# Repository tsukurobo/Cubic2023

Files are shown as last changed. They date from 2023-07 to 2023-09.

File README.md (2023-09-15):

**目次**

- [Cubic2023](#cubic2023)
  - [概要](#概要)
    - [コメント](#コメント)
- [Cubic2023\_Shield](#cubic2023_shield)
  - [概要](#概要-1)
    - [encoder pull up](#encoder-pull-up)
    - [increment encoder cognition](#increment-encoder-cognition)
    - [inverter(NOT)](#inverternot)
    - [increment RP2040](#increment-rp2040)
    - [increment connecter](#increment-connecter)
    - [absolute encoder cognition](#absolute-encoder-cognition)
    - [absolute RP2040](#absolute-rp2040)
    - [absolute connector](#absolute-connector)
    - [decoupling capacitor](#decoupling-capacitor)
    - [Arduino nano 33 BLE](#arduino-nano-33-ble)
    - [to MotherBoard](#to-motherboard)
- [Cubic2023\_DCMotorDriver](#cubic2023_dcmotordriver)
  - [概要](#概要-2)
    - [connector](#connector)
    - [pull down](#pull-down)
    - [A3921](#a3921)
    - [current sensor](#current-sensor)
    - [Filter](#filter)
    - [DeadTime](#deadtime)
    - [Protection Circuit](#protection-circuit)
    - [for motor connection](#for-motor-connection)
    - [Bootstrap Chargepump](#bootstrap-chargepump)
    - [Indication Circuit](#indication-circuit)
    - [V5 Circuit](#v5-circuit)
    - [Decoupling Condenser](#decoupling-condenser)
    - [Bridge](#bridge)
    - [pull up](#pull-up)
    - [error lamp](#error-lamp)
    - [PS](#ps)
    - [BD63150](#bd63150)
    - [Protection Circuit](#protection-circuit-1)
    - [Indication Circuit](#indication-circuit-1)
    - [VREF](#vref)
    - [for solenoid valve](#for-solenoid-valve)
- [Cubic2023\_RP2040](#cubic2023_rp2040)
  - [概要](#概要-3)
    - [RP2040](#rp2040)
    - [bypass condenser](#bypass-condenser)
    - [surge protection](#surge-protection)
    - [connector](#connector-1)
    - [indicator](#indicator)
    - [RESET switch](#reset-switch)
    - [microUSB](#microusb)
    - [QSPI NOR flash](#qspi-nor-flash)
    - [crystal](#crystal)

# Cubic2023

## 概要
つくばろぼっとサークルではNHK学生ロボコンに向けて統合型基板を製作しており、mainがNHK学生ロボコン2023において使用したバージョンです。
回路図の説明やブロック分けなどが出来ておらず、分かりにくい状態です。※修正中

### コメント
修正中です。8/10程度を目途に進めています。

# Cubic2023_Shield
## 概要
メインマイコンを搭載する基板です。メインマイコンには以下の理由からArduino nano 33 BLE(以下：AN33BLE)を採用しました。
- 32bitマイコン
- 浮動小数点演算ユニット搭載
- 書き込み環境の構築が容易

また、AN33BLEはIMUを搭載している点もメリットです。実際には用いていないため精度は不明ですが、基板面積という点では確実にプラスです。

センサとしては、8つのインクリメンタルエンコーダと8つのアブソリュートエンコーダを接続できるように設計しました。

### encoder pull up
インクリメントエンコーダに接続しているA相B相Z相をプルアップしています。

### increment encoder cognition
インクリメントエンコーダは、Z相の多くの範囲でLOWを返すため、NOT回路によりHIGHになり、LEDが光る仕組みです。Z相をプルアップしてるため、未接続の場合LEDは光りません。A相B相が断線してる場合、LEDは光りますが正常に認識されるとは限りません。何番のエンコーダに接続してるか簡易的に確認するための機能です。

### inverter(NOT)
インクリメントエンコーダの波形を整形するインバータ（バッファ）です。NOT回路と等価なので信号が反転します。A相B相は反転しても大きな影響はないですが、Z相はhighの時間が長くなります。長い信号線を介してセンシングするためチャタリング防止などの観点から挿入しました。また、5VトレラントのICを介することで5V信号を3.3Vで駆動するRP2040に入力できるようにしています。

### increment RP2040
インクリメントエンコーダを読み取り値を記録、メインマイコンの要求に応じて状態を返すためのマイコンです。インクリメントエンコーダの読み取りは割り込み処理を必要とするため、メインマイコンと分離したいと考え、この設計にしました。

### increment connecter
ラッチ付かつサイズが小さいコネクタが望ましかったため、PAコネクタを採用しました。**AMT102/103**を接続することを想定して、ピンの順番を設定しています。

### absolute encoder cognition
アブソリュートエンコーダとのSPI通信が確立した場合にRP2040がGPIOを操作しLEDを点灯させることが出来るようにしました。

### absolute RP2040
アブソリュートエンコーダと通信をして値を記録、メインマイコンの要求に応じて状態を返すためのマイコンです。メインマイコンをmasterとしたSPIバスとは別に、absolute RP2040をmasterとしたエンコーダとの通信用のSPIバスを用意しています。

### absolute connector
こちらもPAコネクタを採用しています。**AMT223**を接続することを想定して、ピンの順番を設定しています。

### decoupling capacitor
基板上のICなどのバイパスコンデンサです。配線を引き延ばすためエンコーダのコネクタ近くにも配置しました。

### Arduino nano 33 BLE
メインマイコンです。enableをHIGHにすることでシステムを起動することができます。RESETをLOWにすることでエンコーダ用のRP2040をリセットさせることできます。他はSPI通信用のGPIOです。

### to MotherBoard
電源、SPI通信、シャットダウン信号を共有しています。

### emergency shutdown
緊急停止スイッチ接続することでシステムを起動できます。LEDにより起動状態を表示しています。

### 3-state buffer
SPI通信のslave側は通信していないときはMISOをオープンにする仕様ですが、RP2040はLOWを出力してしまい、複数slave運用がデフォルトで不可能であったため、3-state bufferを付加することで対策しました。

# Cubic2023_DCMotorDriver
## 概要
RZ-735クラスのDCモータを2基、RS-555クラスのDCモータを1基、24Vで駆動することが出来る基板です。以下ではRZ-735を想定したチャネルをメインチャネル、他方をサブチャネルと呼称します。

メインチャネルではICにA3921を採用しています。サブチャネルではICにBD63150を採用しています。データシートを参考に作成しました。データシートに載っている内容は説明を省略します。

サブチャネルはハーフブリッジ×2と見なすことで電磁弁を制御することも出来ます。

https://www.allegromicro.com/ja-jp/products/motor-drivers/brush-dc-motor-drivers/a3921

https://www.rohm.co.jp/products/motor-actuator-drivers/dc-brush-motor/bd63150afm-product

### connector
電流センサのアナログ値伝送用に4pin、信号・降圧電源用に14pin、VDDとGNDPWRに各14pinでMotherBoardと接続します。GNDは信号用と電源用で分離しています。

### pull down
MotherBoardからの信号がない場合の誤動作防止のためにプルダウン抵抗を挿入しています。

### A3921
Cissの大きいMOSFETを容易に駆動できる便利なICです。SR,PWMLにhighを入力、pwmhにPWM、phaseにhigh/lowを入力することで、SMB方式でモータを駆動できます。

### current sensor
メインチャネルを電流制御するために搭載した電流センサICです。コスト面からACS712を採用しましたが、動作を確認したところ、ノイズの影響で大きかったため、現状電流を用いた制御は実装していません。

### Filter
MotherBoardに大容量の電解コンデンサを搭載していますが、ピンヘッダを経由するため補助として中容量の電解コンデンサを搭載しています。

### DeadTime
$$ 50+\frac{7200}{1.2+(200/Rdead[kΩ])} $$
datasheet上の数式に従いdeadtimeが2300nsになるように抵抗値を設定しました。

### Protection Circuit
RCスナバ回路と双方向ツェナーダイオードによる保護回路を搭載しています。RCスナバ回路の値は以下の式に基づいて決定しました。回路を解析して搭載したわけではなく、簡易的な計算から求めているため効果は薄いと思います。

$$ Rsnb = \frac{Vin}{Iin} = \frac{24[V]}{2.4[A]} = 10[Ω] $$
$$ Csnb = \frac{Prsnb}{f×{Vin}^2} = \frac{0.1[W]}{60k[Hz]×{24[V]}^2} = 2.89n[F] $$

$$ Iin:想定電流, Prsnb：スナバ抵抗の定格電力, f:MD動作周波数$$
※想定電流は実際より小さめ、MD動作周波数は実際より大きめの値で計算されてます。設計初期の名残です。

モーターの逆起電力からMDを保護するために降伏電圧が28Vの双方向ツェナーダイオード（TVS）を採用しています。

**注：現行基板では、逆起電力から保護しきれていないことが原因と思われるA3921の破壊が確認されています。**

### for motor connection
モーターに接続する端子です。

### Bootstrap Chargepump
DCバイアスを考慮してコンデンサを配置しました。

### Indication Circuit
モーターに接続している箇所にLEDを対面配置することで回転方向を表示しています。プログラム開発時に便利でした。ローサイドMOSFETのゲート端子にデバッグ用のLEDを配置しています。ICが壊れた場合に表示されなくなるのでデバッグに活用できました。

|  LEDの色  |  用途  |
| ---- | ---- |
|  緑  |  常時点灯  |
|  青  |  電源ON＆正常時点灯  |
|  赤  |  異常時点灯  |
|  黄  |  状態表示  |
|  白  |  状態表示  |

### V5 Circuit
A3921に搭載されている5Vレギュレータを利用してA3921搭載のエラーLEDを配置しています。また、VDSTHに送る電圧を分圧で生成しています。

### Decoupling Condenser
ブートストラップコンデンサの容量が大きく、A3921の挙動が不安定になることがあったので、10uFのコンデンサを搭載しました。

### Bridge
フルブリッジ回路です。前述のRCスナバ回路を搭載しています。MOSFETは**RJ1L12BGN**を採用しています。corestaffで購入すると比較的安価に購入可能です。ON抵抗は小さいですが、ゲート容量は大きいので気を付けてください。新規設計する場合は**RS6L120BG**がおすすめです。ゲート抵抗には27Ωを採用しました。この抵抗値にした理由は勘です。

簡易的ではありますが以下の式で計算可能です。
$$ \frac{Vg}{Imax} < Rg < \frac{Tdead}{3×Ciss}$$
$$ Rg:ゲート抵抗,Vg:ゲート駆動電圧,Imax:ICがゲートに流せる最大電流,Tdead:デッドタイム,Ciss:MOSFET入力容量　$$
※条件によっては解なしになるかと思います。

### pull up
MDへの入力信号をプルアップしています。

### error lamp
BD63150のエラー表示用のLEDです。

### PS
PowerSaveに繋いでる端子です。プルアップしています。

### BD63150
電圧制御・電流制限に対応したモータードライバICです。RFNには100mΩのシャント抵抗を搭載しています。3Aで電流制限をする計算でしたが、想定より厳しめに作動していました。恐らくGNDを信号とパワーで分離した弊害だと思われます。

### Protection Circuit
メインチャネルと同様の構成です。

### Indication Circuit
メインチャネルと同様の構成です。

### VREF
電流の制限値をICに入力するピンです。3Aで制限するように設定したのですが、前述の通り思うように動きませんでした。

### for solenoid valve
電磁弁を駆動できるように付加した回路です。セーフティとしてリセッタブルヒューズを載せています。また還流ダイオードも載せています。

# Cubic2023_RP2040
## 概要
Cubicでは以下の理由から組み込みマイコンにRP2040を採用しました。
- GPIOとPWMが多い
- cortex-M0（計算速度がそこそこ速い）
- 安価
- 書き込みが容易

システム内で3つ使い、容易に交換可能とするためにマイコンボードとして最小構成の基板を作成しました。

以下の公式リファレンスを参考に作成しました。公式リファレンスに載っている内容は説明を省略します。
https://datasheets.raspberrypi.com/rp2040/hardware-design-with-rp2040.pdf

### RP2040
RP2040と周辺の配線です。
### bypass condenser
マイコンの電力消費が多く動作が不安定になることがあったため、100uFのセラコンを追加しています。
### surge protection
システム内でモータドライバと絶縁せずにRP2040を用いている箇所があるため、サージ保護としてツェナーダイオードを電源に並列に繋いでいます。
### connector
基板サイズの制約の中でGPIOをフルに使う必要があり、1.27mmピッチのピンヘッダを採用しました。配線の最適化と差し込みの一意性を担保するために基板の3辺に沿うように配置しています。
### indicator
基板内通信にSPIを利用しているのですが、SPI通信の状態を外部から容易に観測するためにslave側のSSに該当する箇所にLEDを付けています。以下は目視のLED状態とSSに注意したSPI通信の状況です。
|  LED  |  状況  |
| ---- | ---- |
|  点灯  |  通信異常  |
|  僅かに点灯  |  正常  |
|  点滅  |  通信速度低  |
|  消灯  |  オフライン  |

### RESET switch
RP2040をリセットできます。接続先がMotherBoardの場合は、接続先もリセットされます。

### microUSB
RP2040にプログラムを書き込むmicroUSBです。基本的に動作中の電源は接続先の基板から受け取るため、RP2040に書き込む以外は使用しない想定です。

### QSPI NOR flash
プログラムが書き込まれるメモリです。

### crystal
RP2040動作のためのcrystalです。

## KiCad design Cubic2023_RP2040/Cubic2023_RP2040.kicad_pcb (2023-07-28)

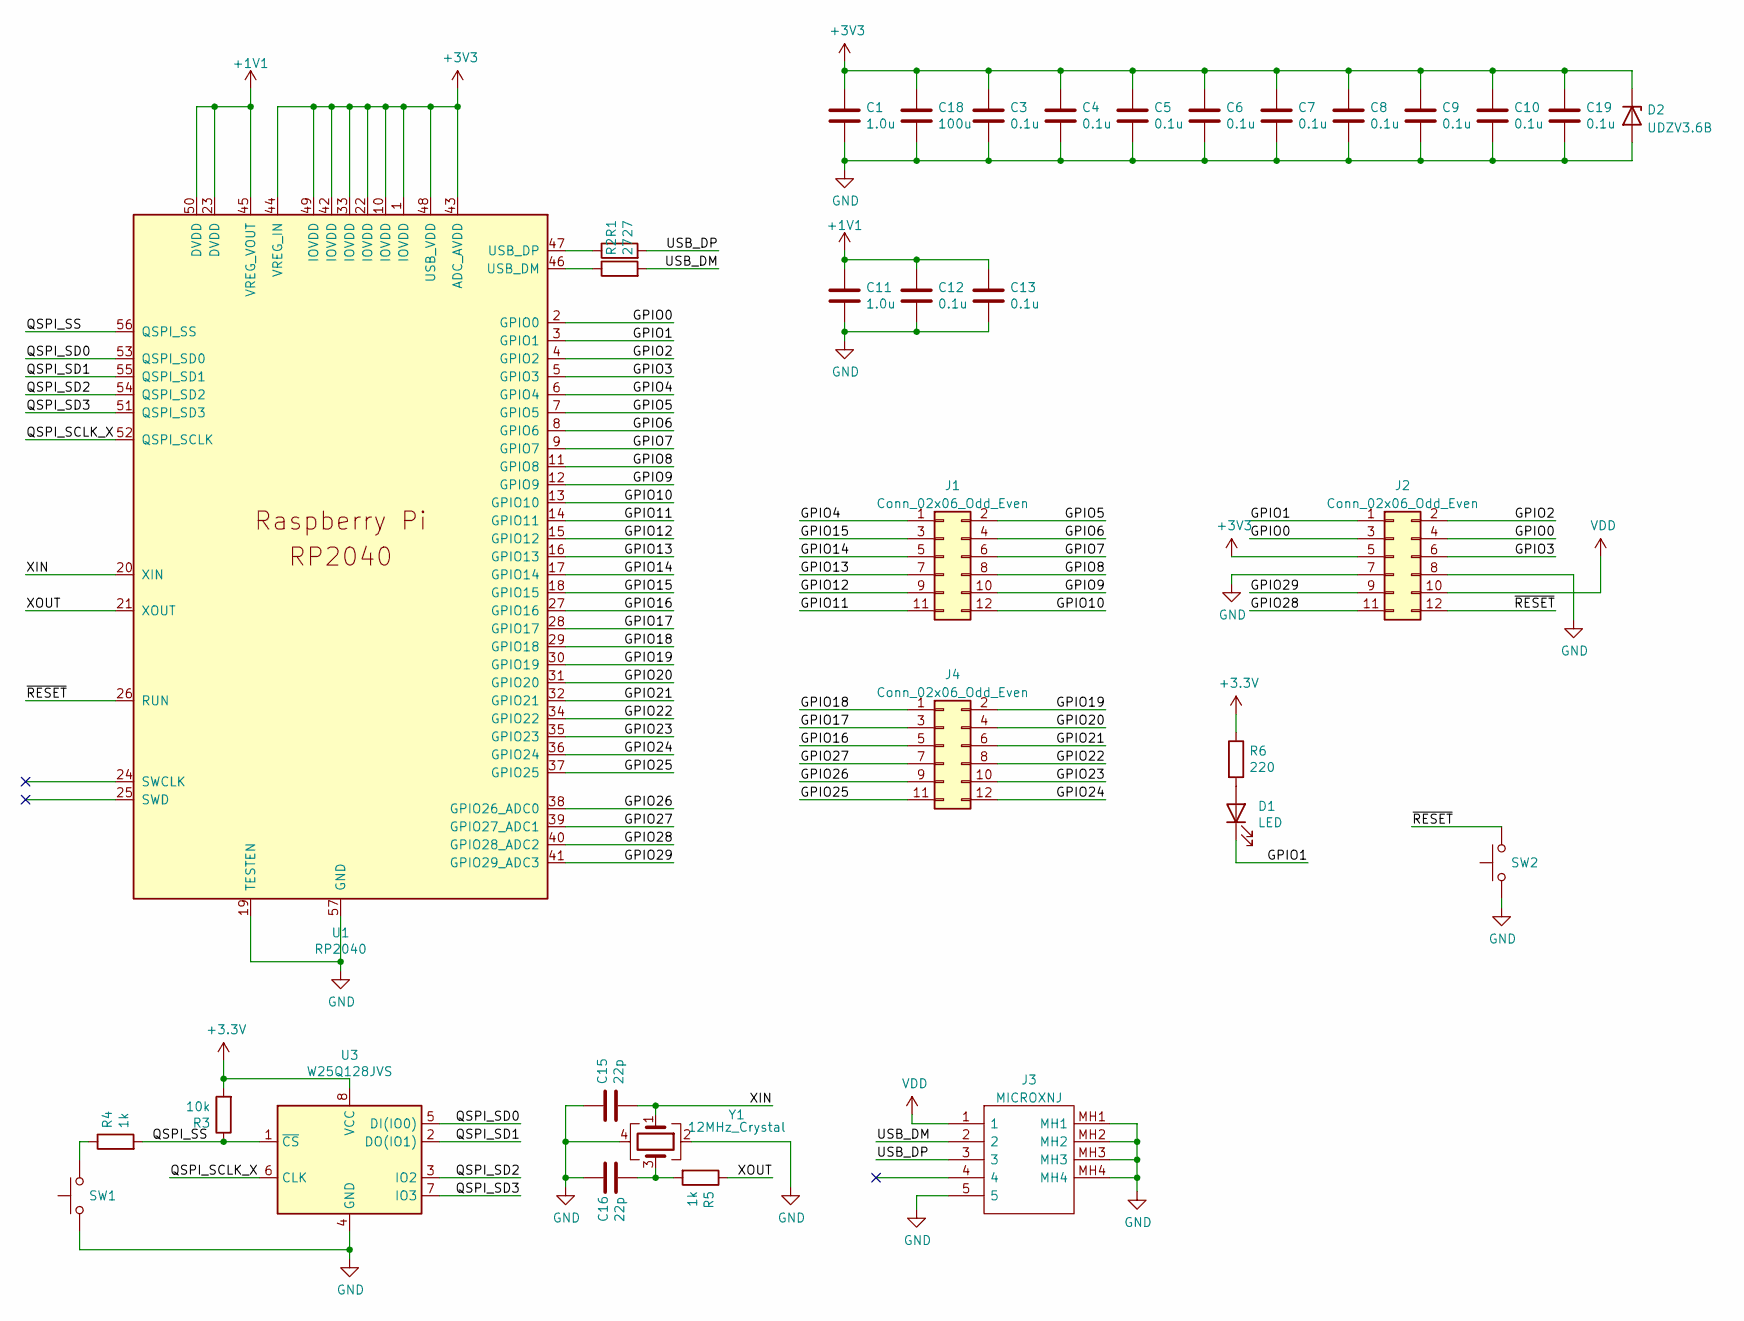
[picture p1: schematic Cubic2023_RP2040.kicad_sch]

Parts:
C1, C11: 1.0u; C_0805_2012Metric; LCSC C28323
C3, C4, C5, C6, C7, C8, C9, C10, C12, C13, C19: 0.1u; C_0402_1005Metric_Pad0.74x0.62mm_HandSolder; LCSC C307331
C15, C16: 22p; C_0402_1005Metric_Pad0.74x0.62mm_HandSolder; LCSC C1555
C18: 100u; C_1206_3216Metric; LCSC C15008
D1: LED; LED_0603_1608Metric_Pad1.05x0.95mm_HandSolder; LCSC C72041
D2: UDZV3.6B; D_SOD-323_HandSoldering
J1, J2, J4: Conn_02x06_Odd_Even; PinHeader_2x06_P1.27mm_Vertical
J3: MICROXNJ; Manufacturer_Part_Number MICROXNJ; LCSC C404969
R1, R2: 27; R_0603_1608Metric; LCSC C25190
R3: 10k; R_0603_1608Metric; LCSC C25804
R4, R5: 1k; R_0603_1608Metric; LCSC C21190
R6: 220; R_0603_1608Metric; LCSC C22962
SW1, SW2: SW_Push; SW_DIP_SPSTx01_Slide_9.78x4.72mm_W7.62mm_P2.54mm
U1: RP2040; RP2040-QFN-56; LCSC C2040
U3: W25Q128JVS; SOIC-8_5.23x5.23mm_P1.27mm; LCSC C97521
Y1: 12MHz_Crystal; Crystal_SMD_3225-4Pin_3.2x2.5mm; LCSC C9002

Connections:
+1V1: C11.1, C12.1, C13.1, U1.23 (DVDD), U1.45 (VREG_VOUT), U1.50 (DVDD)
/GPIO0: J2.3, J2.4, U1.2 (GPIO0)
/GPIO1: D1.1 (K), J2.1, U1.3 (GPIO1)
/GPIO2: J2.2, U1.4 (GPIO2)
/GPIO3: J2.6, U1.5 (GPIO3)
/GPIO4: J1.1, U1.6 (GPIO4)
/GPIO5: J1.2, U1.7 (GPIO5)
/GPIO6: J1.4, U1.8 (GPIO6)
/GPIO7: J1.6, U1.9 (GPIO7)
/GPIO8: J1.8, U1.11 (GPIO8)
/GPIO9: J1.10, U1.12 (GPIO9)
/GPIO10: J1.12, U1.13 (GPIO10)
/GPIO11: J1.11, U1.14 (GPIO11)
/GPIO12: J1.9, U1.15 (GPIO12)
/GPIO13: J1.7, U1.16 (GPIO13)
/GPIO14: J1.5, U1.17 (GPIO14)
/GPIO15: J1.3, U1.18 (GPIO15)
/GPIO16: J4.5, U1.27 (GPIO16)
/GPIO17: J4.3, U1.28 (GPIO17)
/GPIO18: J4.1, U1.29 (GPIO18)
/GPIO19: J4.2, U1.30 (GPIO19)
/GPIO20: J4.4, U1.31 (GPIO20)
/GPIO21: J4.6, U1.32 (GPIO21)
/GPIO22: J4.8, U1.34 (GPIO22)
/GPIO23: J4.10, U1.35 (GPIO23)
/GPIO24: J4.12, U1.36 (GPIO24)
/GPIO25: J4.11, U1.37 (GPIO25)
/GPIO26: J4.9, U1.38 (GPIO26_ADC0)
/GPIO27: J4.7, U1.39 (GPIO27_ADC1)
/GPIO28: J2.11, U1.40 (GPIO28_ADC2)
/GPIO29: J2.9, U1.41 (GPIO29_ADC3)
/QSPI_SCLK_X: U1.52 (QSPI_SCLK), U3.6 (CLK)
/QSPI_SD0: U1.53 (QSPI_SD0), U3.5 (DI(IO0))
/QSPI_SD1: U1.55 (QSPI_SD1), U3.2 (DO(IO1))
/QSPI_SD2: U1.54 (QSPI_SD2), U3.3 (IO2)
/QSPI_SD3: U1.51 (QSPI_SD3), U3.7 (IO3)
/QSPI_SS: R3.1, R4.2, U1.56 (QSPI_SS), U3.1 (~CS)
/USB_DM: J3.2, R2.2
/USB_DP: J3.3, R1.2
/XIN: C15.2, U1.20 (XIN), Y1.1
/XOUT: R5.1, U1.21 (XOUT)
/~RESET: J2.12, SW2.2, U1.26 (RUN)
GND: C1.2, C3.2, C4.2, C5.2, C6.2, C7.2, C8.2, C9.2, C10.2, C11.2, C12.2, C13.2, C15.1, C16.1, C18.2, C19.2, D2.2 (A), J2.7, J2.8, J3.5, J3.MH1, J3.MH2, J3.MH3, J3.MH4, SW1.1, SW2.1, U1.19 (TESTEN), U1.57 (GND), U3.4 (GND), Y1.2, Y1.4
unnamed: D1.2 (A), R6.2
unnamed: R1.1, U1.47 (USB_DP)
unnamed: R2.1, U1.46 (USB_DM)
unnamed: R4.1, SW1.2
unnamed: C16.2, R5.2, Y1.3
VDD: J2.10, J3.1

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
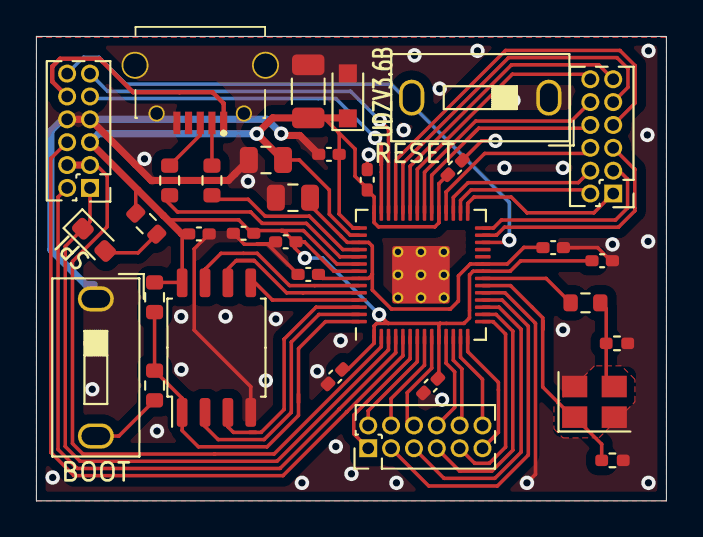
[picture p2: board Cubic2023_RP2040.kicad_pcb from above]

Board: 2 copper layers, 35.0 x 25.8 mm, 33 parts (0 on the bottom side), 50 nets.

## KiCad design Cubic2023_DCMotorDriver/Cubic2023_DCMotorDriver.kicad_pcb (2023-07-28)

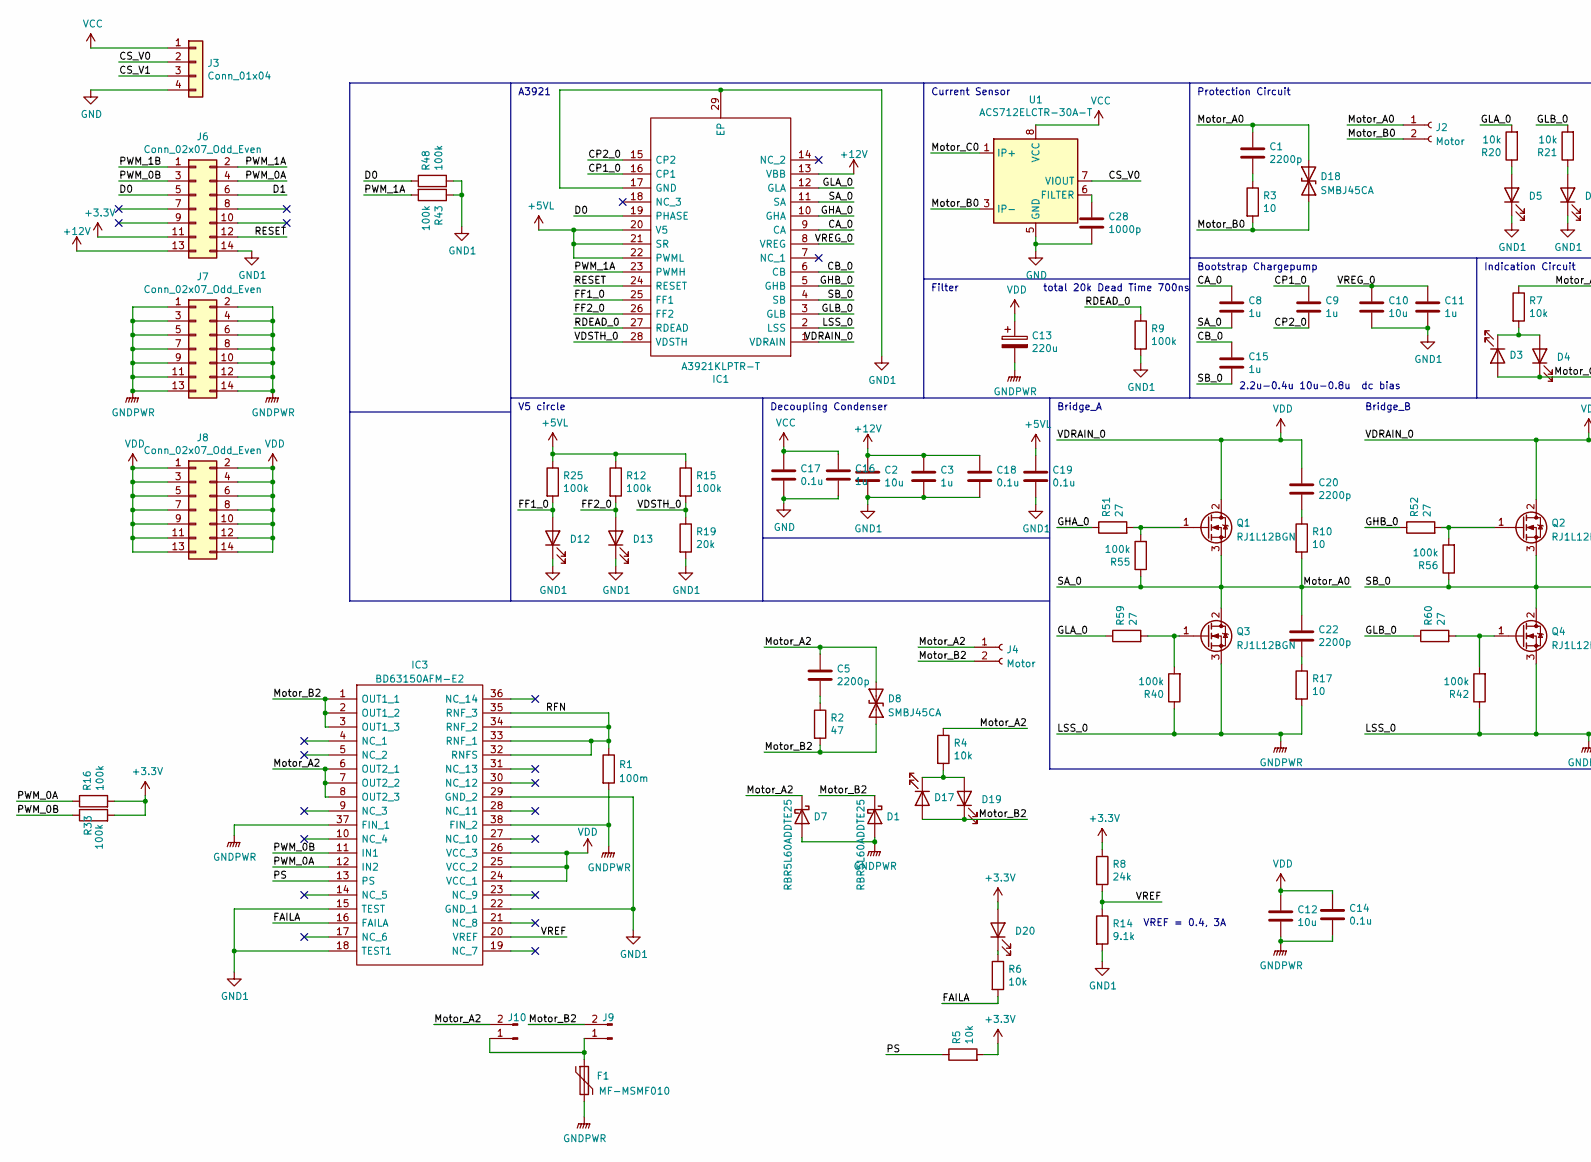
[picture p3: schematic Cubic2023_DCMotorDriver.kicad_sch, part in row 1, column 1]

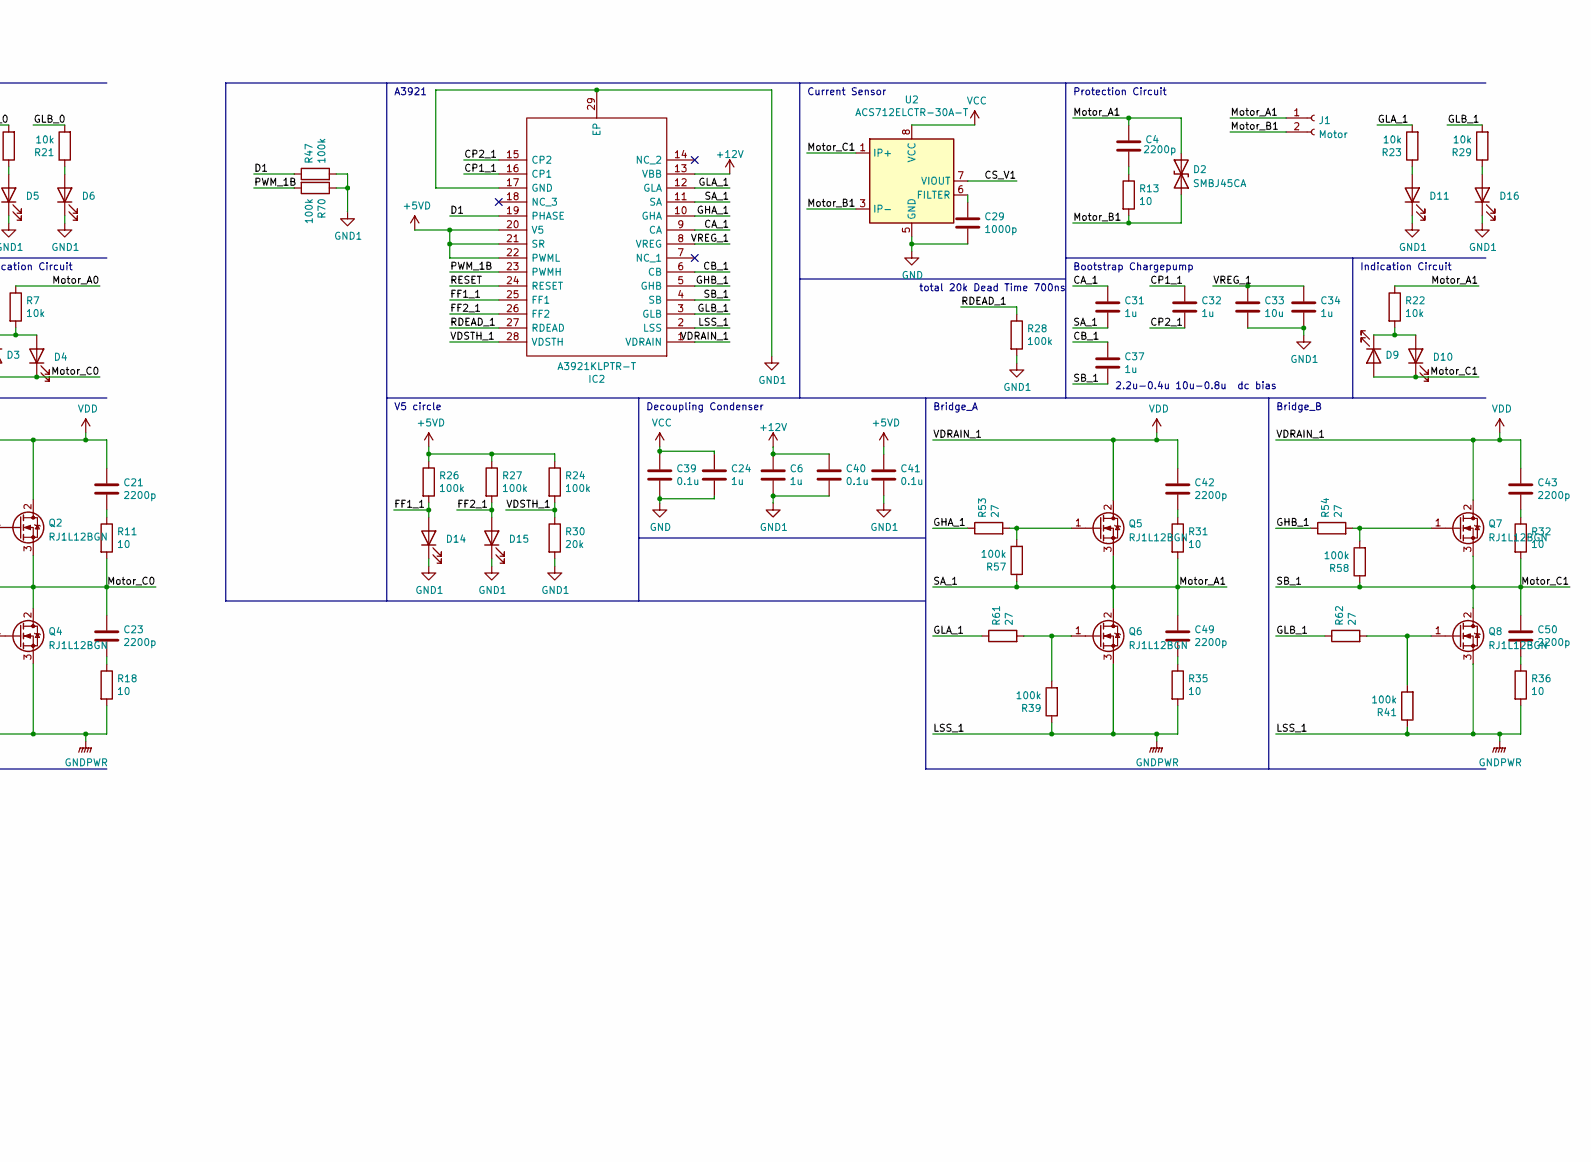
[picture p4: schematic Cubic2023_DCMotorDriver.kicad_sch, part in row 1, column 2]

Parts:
C1, C4, C5, C20, C21, C22, C23, C42, C43, C49, C50: 2200p; R_0603_1608Metric; LCSC C1604
C2, C10, C12, C33: 10u; C_1206_3216Metric; LCSC C13585
C3, C6, C8, C9, C11, C15, C16, C24, C31, C32, C34, C37: 1u; R_0603_1608Metric; LCSC C15849
C13: 220u; CP_Elec_10x10.5
C14, C17, C18, C19, C39, C40, C41: 0.1u; C_0402_1005Metric_Pad0.74x0.62mm_HandSolder; LCSC C307331
C28, C29: 1000p; R_0603_1608Metric; LCSC C1588
D1, D7: RBR5L60ADDTE25; D_SMA
D2, D8, D18: SMBJ45CA; D_SMB; LCSC C353357
D3, D9, D17: LED_White; D_0603_1608Metric_Pad1.05x0.95mm_HandSolder; LCSC C2290
D4, D10, D19: LED_Yellow; D_0603_1608Metric_Pad1.05x0.95mm_HandSolder; LCSC C72038
D5, D6, D11, D16: LED_Blue; D_0603_1608Metric_Pad1.05x0.95mm_HandSolder; LCSC C72041
D12, D13, D14, D15, D20: LED_Red; D_0603_1608Metric_Pad1.05x0.95mm_HandSolder; LCSC C2286
F1: MF-MSMF010; Fuse_1812_4532Metric; LCSC C12430
IC1, IC2: A3921KLPTR-T; HTSSOP-28-1EP_4.4x9.7mm_P0.65mm_EP2.85x5.4mm_ThermalVias; Manufacturer_Part_Number A3921KLPTR-T
IC3: BD63150AFM-E2; BD63150AFME2; Manufacturer_Part_Number BD63150AFM-E2; Mouser Part Number 755-BD63150AFM-E2
J1, J2, J4: Motor; T_plug_female
J3: Conn_01x04; PinHeader_1x04_P2.54mm_Horizontal
J6, J7, J8: Conn_02x07_Odd_Even; PinHeader_2x07_P2.54mm_Horizontal
J9, J10: Conn_01x02_Male; PinHeader_1x02_P2.00mm_Horizontal
Q1, Q2, Q3, Q4, Q5, Q6, Q7, Q8: RJ1L12BGN; TO-263-2
R1: 100m; R_2512_6332Metric; LCSC C2994646
R2: 47; R_0603_1608Metric; LCSC C23182
R3, R10, R11, R13, R17, R18, R31, R32, R35, R36: 10; R_0603_1608Metric; LCSC C22859
R4, R5, R6, R7, R20, R21, R22, R23, R29: 10k; R_0603_1608Metric; LCSC C25804
R8: 24k; R_0603_1608Metric; LCSC C23352
R9, R12, R15, R16, R24, R25, R26, R27, R28, R33, R39, R40, R41, R42, R43, R47, R48, R55, R56, R57, R58, R70: 100k; R_0603_1608Metric; LCSC C25803
R14: 9.1k; R_0603_1608Metric; LCSC C23260
R19, R30: 20k; R_0603_1608Metric; LCSC C4184
R51, R52, R53, R54, R59, R60, R61, R62: 27; R_0603_1608Metric; LCSC C25190
U1, U2: ACS712ELCTR-30A-T; SOP-8_3.9x4.9mm_P1.27mm

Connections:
+3V3: D20.2 (A), J6.11, R5.2, R8.1, R16.2, R33.2
+5VD: C41.1, IC2.20 (V5), IC2.21 (SR), IC2.22 (PWML), R24.1, R26.1, R27.1
+5VL: C19.1, IC1.20 (V5), IC1.21 (SR), IC1.22 (PWML), R12.1, R15.1, R25.1
+12V: C2.1, C3.1, C6.1, C18.1, C40.1, IC1.13 (VBB), IC2.13 (VBB), J6.13
/CA_0: C8.1, IC1.9 (CA)
/CA_1: C31.1, IC2.9 (CA)
/CB_0: C15.1, IC1.6 (CB)
/CB_1: C37.1, IC2.6 (CB)
/CP1_0: C9.1, IC1.16 (CP1)
/CP1_1: C32.1, IC2.16 (CP1)
/CP2_0: C9.2, IC1.15 (CP2)
/CP2_1: C32.2, IC2.15 (CP2)
/CS_V0: J3.2, U1.7 (VIOUT)
/CS_V1: J3.3, U2.7 (VIOUT)
/D0: IC1.19 (PHASE), J6.5, R48.1
/D1: IC2.19 (PHASE), J6.6, R47.1
/FAILA: IC3.16 (FAILA), R6.2
/FF1_0: D12.2 (A), IC1.25 (FF1), R25.2
/FF1_1: D14.2 (A), IC2.25 (FF1), R26.2
/FF2_0: D13.2 (A), IC1.26 (FF2), R12.2
/FF2_1: D15.2 (A), IC2.26 (FF2), R27.2
/GHA_0: IC1.10 (GHA), R51.1
/GHA_1: IC2.10 (GHA), R53.1
/GHB_0: IC1.5 (GHB), R52.1
/GHB_1: IC2.5 (GHB), R54.1
/GLA_0: IC1.12 (GLA), R20.2, R59.1
/GLA_1: IC2.12 (GLA), R23.2, R61.1
/GLB_0: IC1.3 (GLB), R21.2, R60.1
/GLB_1: IC2.3 (GLB), R29.2, R62.1
/Motor_A0: C1.1, C8.2, C22.1, D18.2 (A2), IC1.11 (SA), J2.1, Q1.3 (S), Q3.2 (D), R7.1, R10.2, R55.1
/Motor_A1: C4.1, C31.2, C49.1, D2.2 (A2), IC2.11 (SA), J1.1, Q5.3 (S), Q6.2 (D), R22.1, R31.2, R57.1
/Motor_A2: C5.1, D7.1 (K), D8.2 (A2), IC3.6 (OUT2_1), IC3.7 (OUT2_2), IC3.8 (OUT2_3), J4.1, J10.2, R4.1
/Motor_B0: D18.1 (A1), J2.2, R3.2, U1.3 (IP-), U1.4 (IP-)
/Motor_B1: D2.1 (A1), J1.2, R13.2, U2.3 (IP-), U2.4 (IP-)
/Motor_B2: D1.1 (K), D8.1 (A1), D17.2 (A), D19.1 (K), IC3.1 (OUT1_1), IC3.2 (OUT1_2), IC3.3 (OUT1_3), J4.2, J9.2, R2.2
/Motor_C0: C15.2, C23.1, D3.2 (A), D4.1 (K), IC1.4 (SB), Q2.3 (S), Q4.2 (D), R11.2, R56.1, U1.1 (IP+), U1.2 (IP+)
/Motor_C1: C37.2, C50.1, D9.2 (A), D10.1 (K), IC2.4 (SB), Q7.3 (S), Q8.2 (D), R32.2, R58.1, U2.1 (IP+), U2.2 (IP+)
/PS: IC3.13 (PS), R5.1
/PWM_0A: IC3.12 (IN2), J6.4, R16.1
/PWM_0B: IC3.11 (IN1), J6.3, R33.1
/PWM_1A: IC1.23 (PWMH), J6.2, R43.2
/PWM_1B: IC2.23 (PWMH), J6.1, R70.2
/RDEAD_0: IC1.27 (RDEAD), R9.1
/RDEAD_1: IC2.27 (RDEAD), R28.1
/RESET: IC1.24 (RESET), IC2.24 (RESET), J6.12
/RFN: IC3.32 (RNFS), IC3.33 (RNF_1), IC3.34 (RNF_2), IC3.35 (RNF_3), R1.1
/VDSTH_0: IC1.28 (VDSTH), R15.2, R19.1
/VDSTH_1: IC2.28 (VDSTH), R24.2, R30.1
/VREF: IC3.20 (VREF), R8.2, R14.1
/VREG_0: C10.1, C11.1, IC1.8 (VREG)
/VREG_1: C33.1, C34.1, IC2.8 (VREG)
GND: C16.2, C17.2, C24.2, C28.2, C29.2, C39.2, J3.4, U1.5 (GND), U2.5 (GND)
GND1: C2.2, C3.2, C6.2, C10.2, C11.2, C18.2, C19.2, C33.2, C34.2, C40.2, C41.2, D5.1 (K), D6.1 (K), D11.1 (K), D12.1 (K), D13.1 (K), D14.1 (K), D15.1 (K), D16.1 (K), IC1.17 (GND), IC1.29 (EP), IC2.17 (GND), IC2.29 (EP), IC3.15 (TEST), IC3.18 (TEST1), IC3.22 (GND_1), IC3.29 (GND_2), J6.14, R9.2, R14.2, R19.2, R28.2, R30.2, R43.1, R47.2, R48.2, R70.1
GNDPWR: C12.2, C13.2, C14.2, D1.2 (A), D7.2 (A), F1.2, IC1.2 (LSS), IC2.2 (LSS), IC3.37 (FIN_1), IC3.38 (FIN_2), J7.1, J7.2, J7.3, J7.4, J7.5, J7.6, J7.7, J7.8, J7.9, J7.10, J7.11, J7.12, J7.13, J7.14, Q3.3 (S), Q4.3 (S), Q6.3 (S), Q8.3 (S), R1.2, R17.2, R18.2, R35.2, R36.2, R39.1, R40.1, R41.1, R42.1
unnamed: C1.2, R3.1
unnamed: C4.2, R13.1
unnamed: C5.2, R2.1
unnamed: C20.2, R10.1
unnamed: C21.2, R11.1
unnamed: C22.2, R17.1
unnamed: C23.2, R18.1
unnamed: C28.1, U1.6 (FILTER)
unnamed: C29.1, U2.6 (FILTER)
unnamed: C42.2, R31.1
unnamed: C43.2, R32.1
unnamed: C49.2, R35.1
unnamed: C50.2, R36.1
unnamed: D3.1 (K), D4.2 (A), R7.2
unnamed: D5.2 (A), R20.1
unnamed: D6.2 (A), R21.1
unnamed: D9.1 (K), D10.2 (A), R22.2
unnamed: D11.2 (A), R23.1
unnamed: D16.2 (A), R29.1
unnamed: D17.1 (K), D19.2 (A), R4.2
unnamed: D20.1 (K), R6.1
unnamed: F1.1, J9.1, J10.1
unnamed: Q1.1 (G), R51.2, R55.2
unnamed: Q2.1 (G), R52.2, R56.2
unnamed: Q3.1 (G), R40.2, R59.2
unnamed: Q4.1 (G), R42.2, R60.2
unnamed: Q5.1 (G), R53.2, R57.2
unnamed: Q6.1 (G), R39.2, R61.2
unnamed: Q7.1 (G), R54.2, R58.2
unnamed: Q8.1 (G), R41.2, R62.2
VCC: C16.1, C17.1, C24.1, C39.1, J3.1, U1.8 (VCC), U2.8 (VCC)
VDD: C12.1, C13.1, C14.1, C20.1, C21.1, C42.1, C43.1, IC1.1 (VDRAIN), IC2.1 (VDRAIN), IC3.24 (VCC_1), IC3.25 (VCC_2), IC3.26 (VCC_3), J8.1, J8.2, J8.3, J8.4, J8.5, J8.6, J8.7, J8.8, J8.9, J8.10, J8.11, J8.12, J8.13, J8.14, Q1.2 (D), Q2.2 (D), Q5.2 (D), Q7.2 (D)

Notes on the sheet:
2.2u-0.4u 10u-0.8u dc bias
Decoupling Condenser
Bootstrap Chargepump
Filter
Current Sensor
Bridge_B
VREF = 0.4, 3A
V5 circle
Bridge_A
Indication Circuit
total 20k Dead Time 700ns
A3921
Protection Circuit

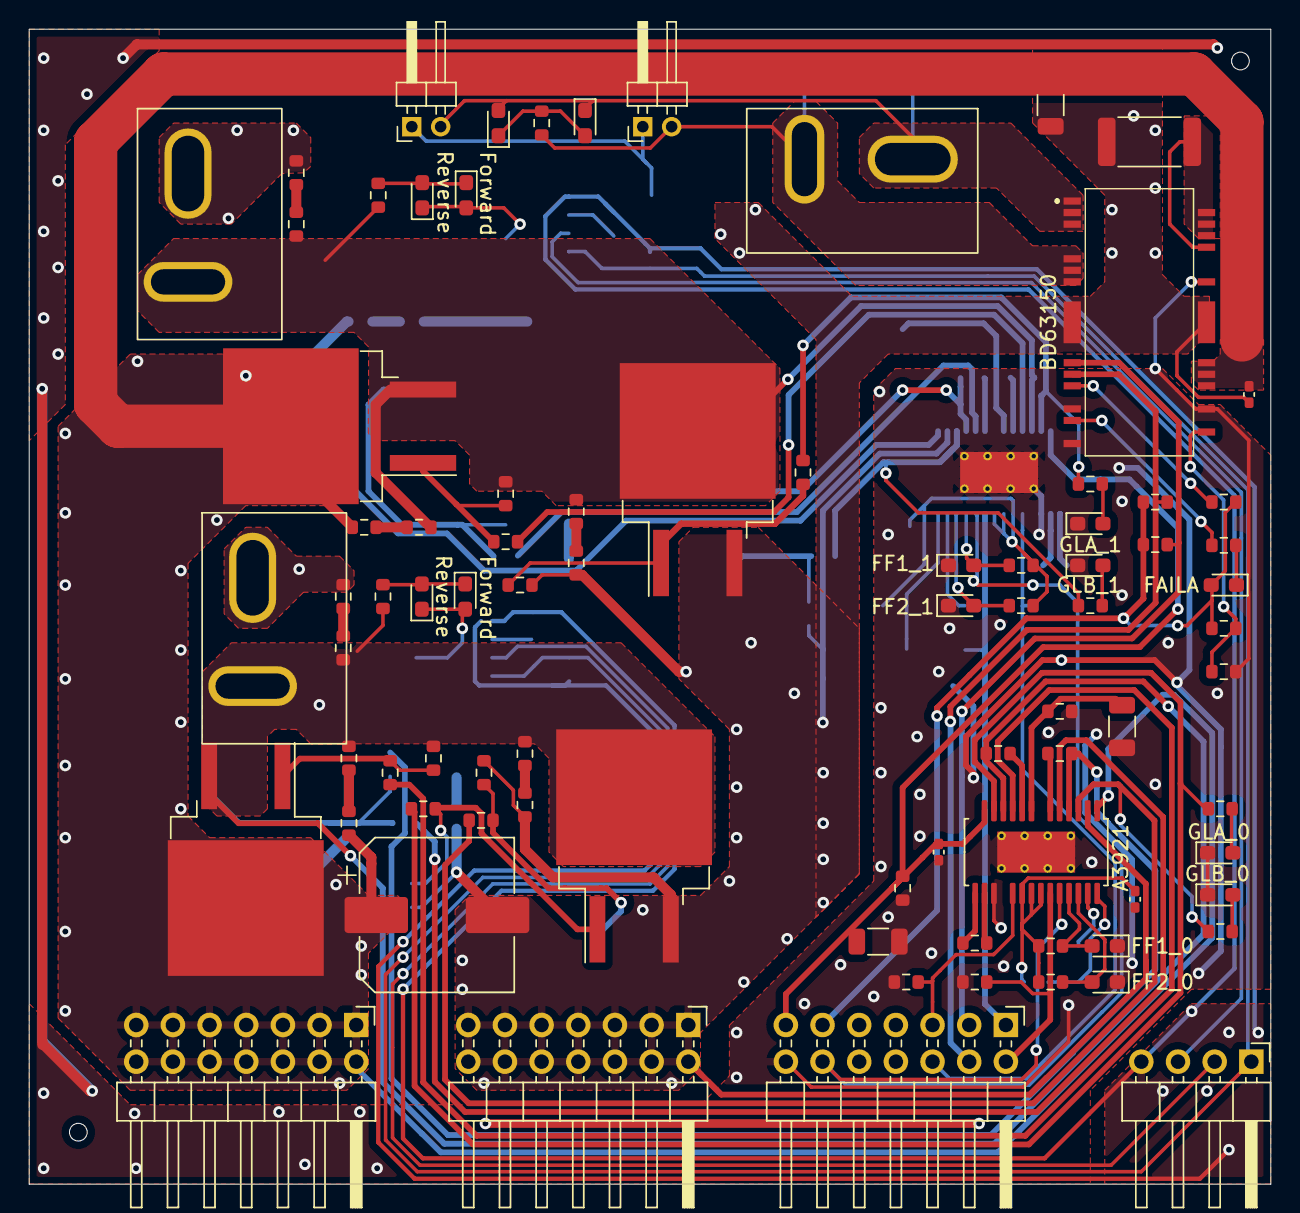
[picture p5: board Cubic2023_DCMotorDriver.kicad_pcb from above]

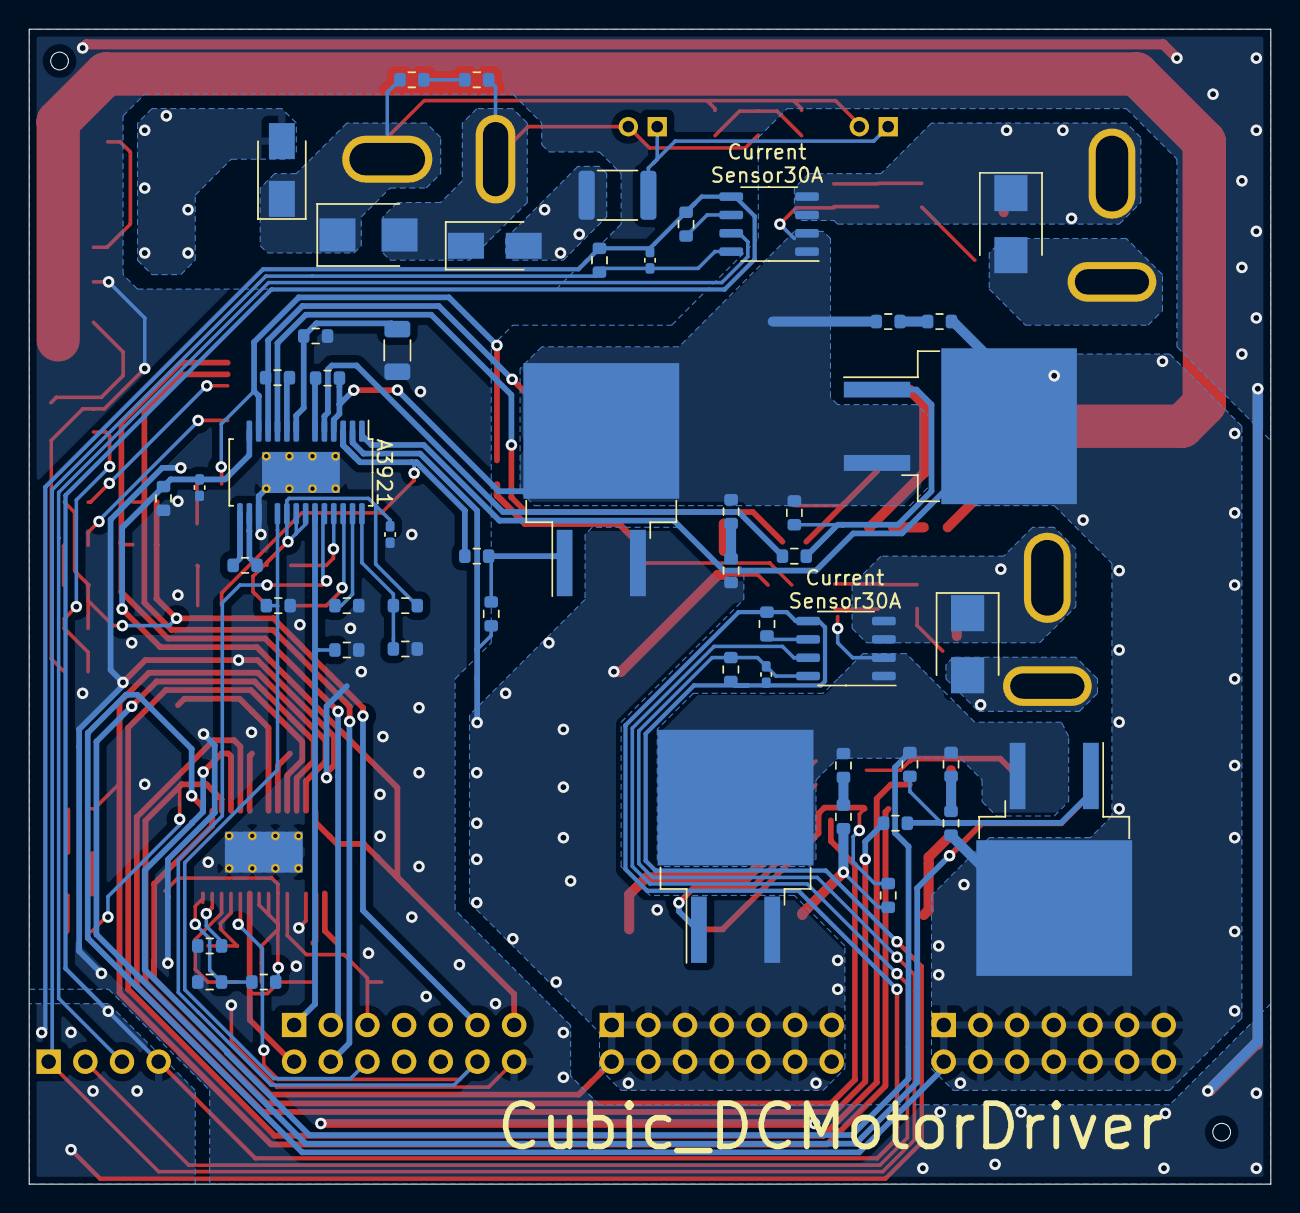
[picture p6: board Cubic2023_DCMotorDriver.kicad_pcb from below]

Board: 2 copper layers, 86.0 x 80.0 mm, 135 parts (52 on the bottom side), 86 nets.

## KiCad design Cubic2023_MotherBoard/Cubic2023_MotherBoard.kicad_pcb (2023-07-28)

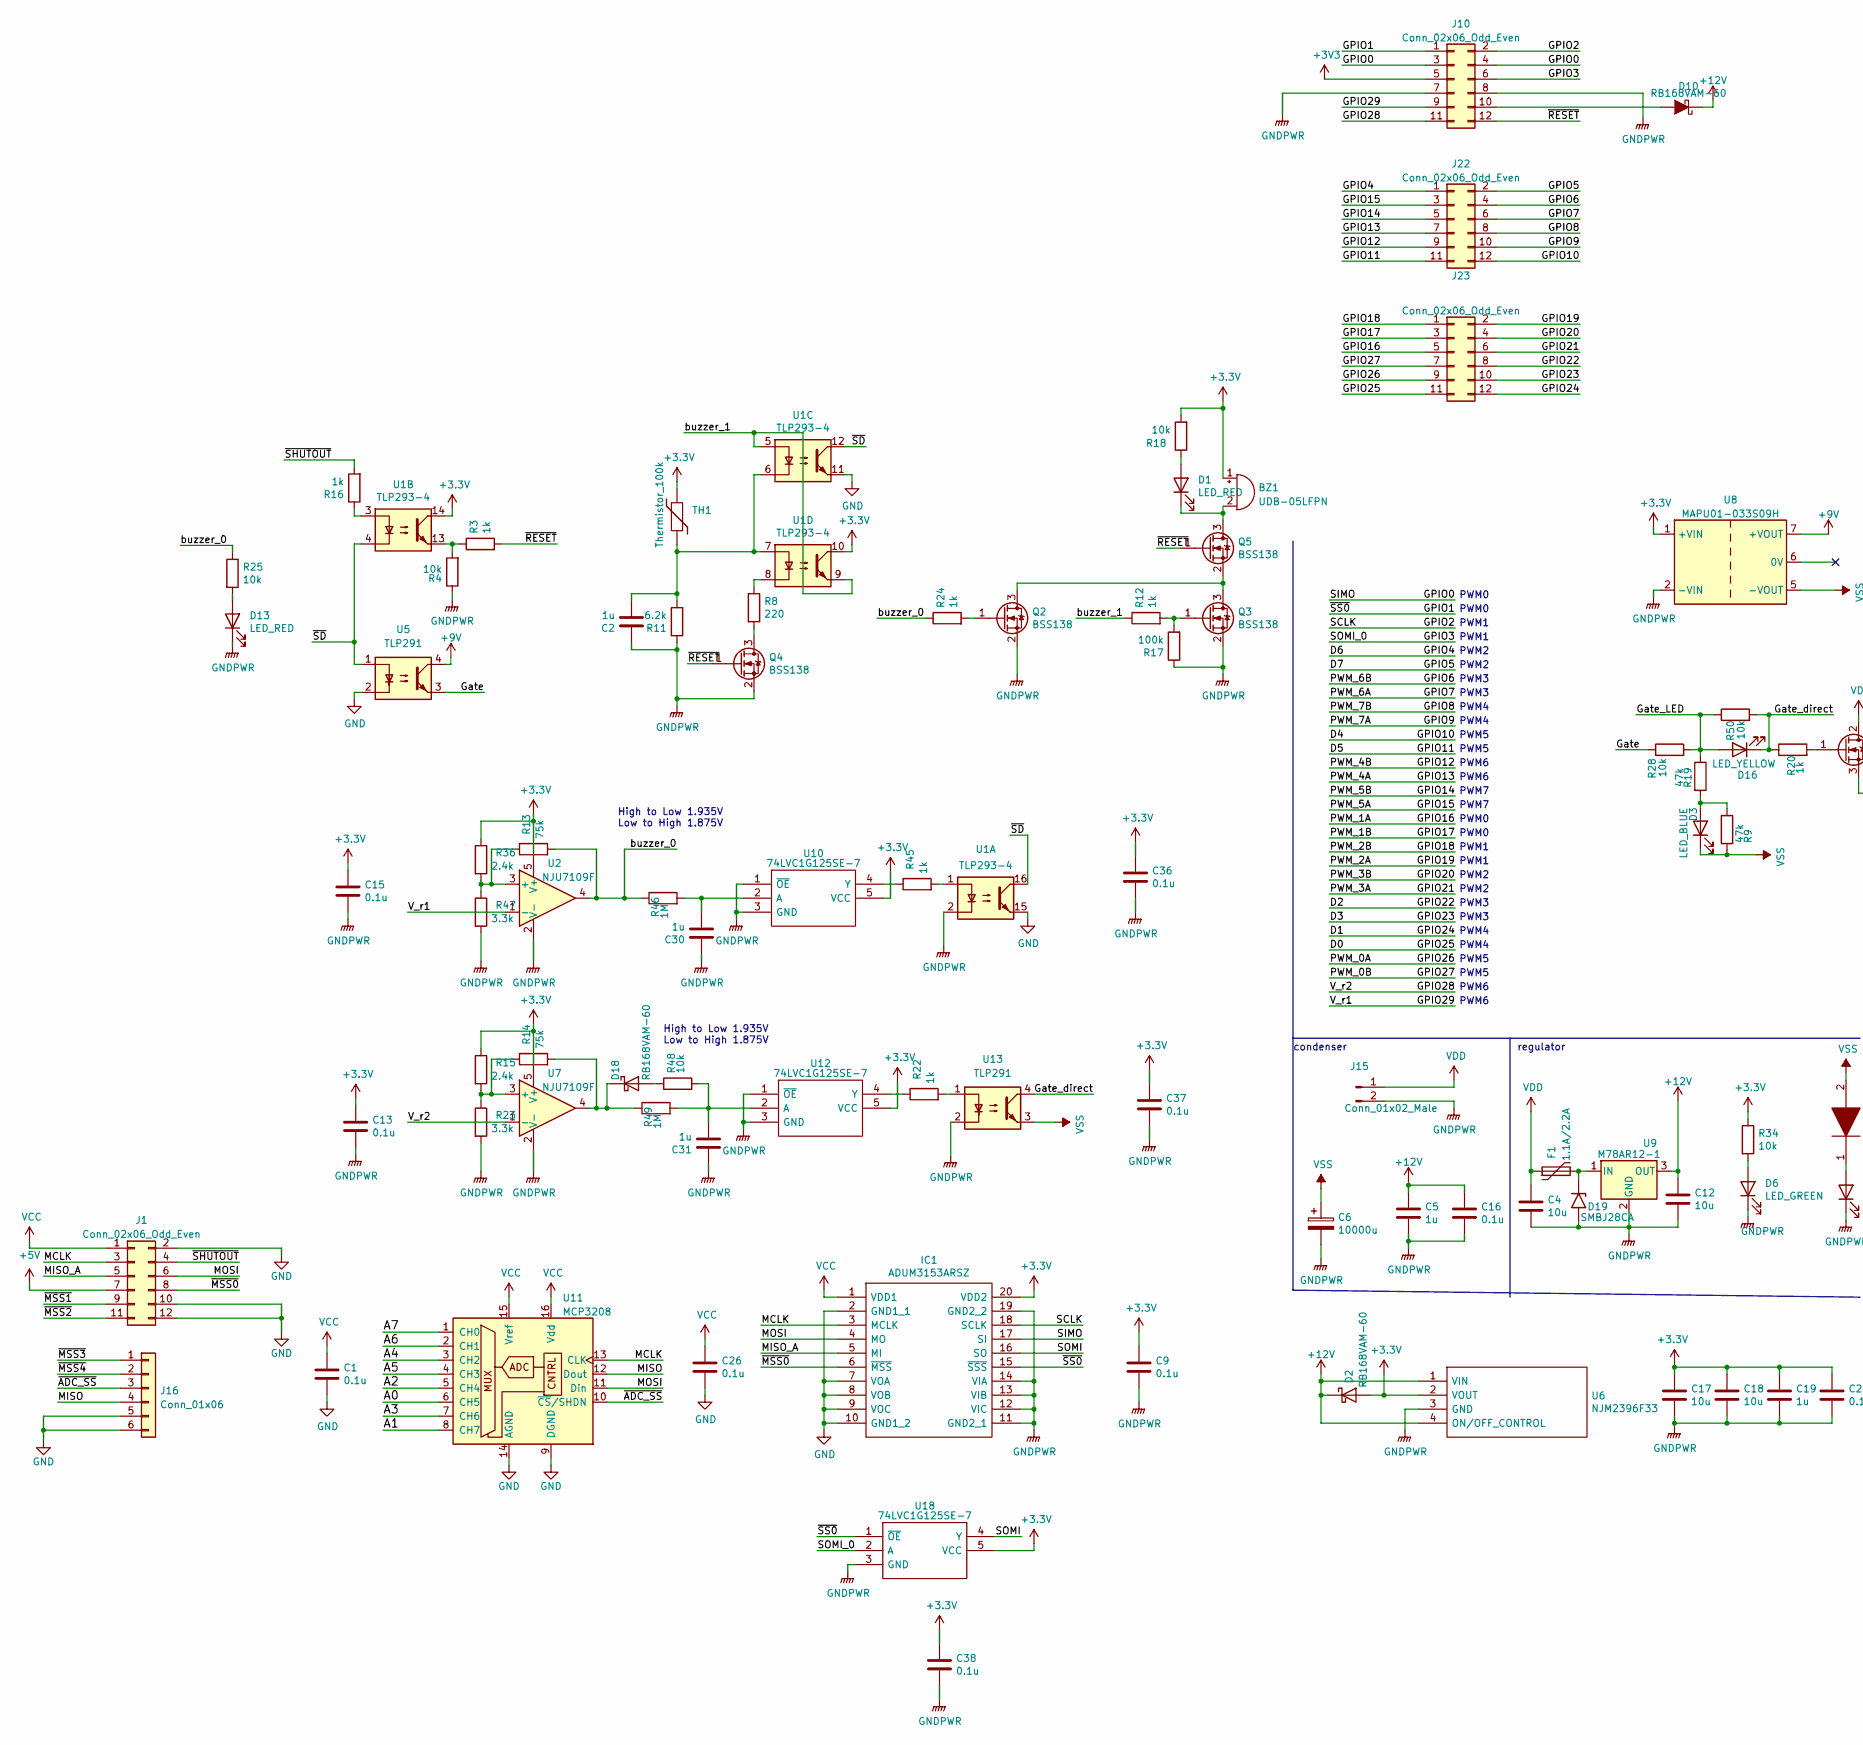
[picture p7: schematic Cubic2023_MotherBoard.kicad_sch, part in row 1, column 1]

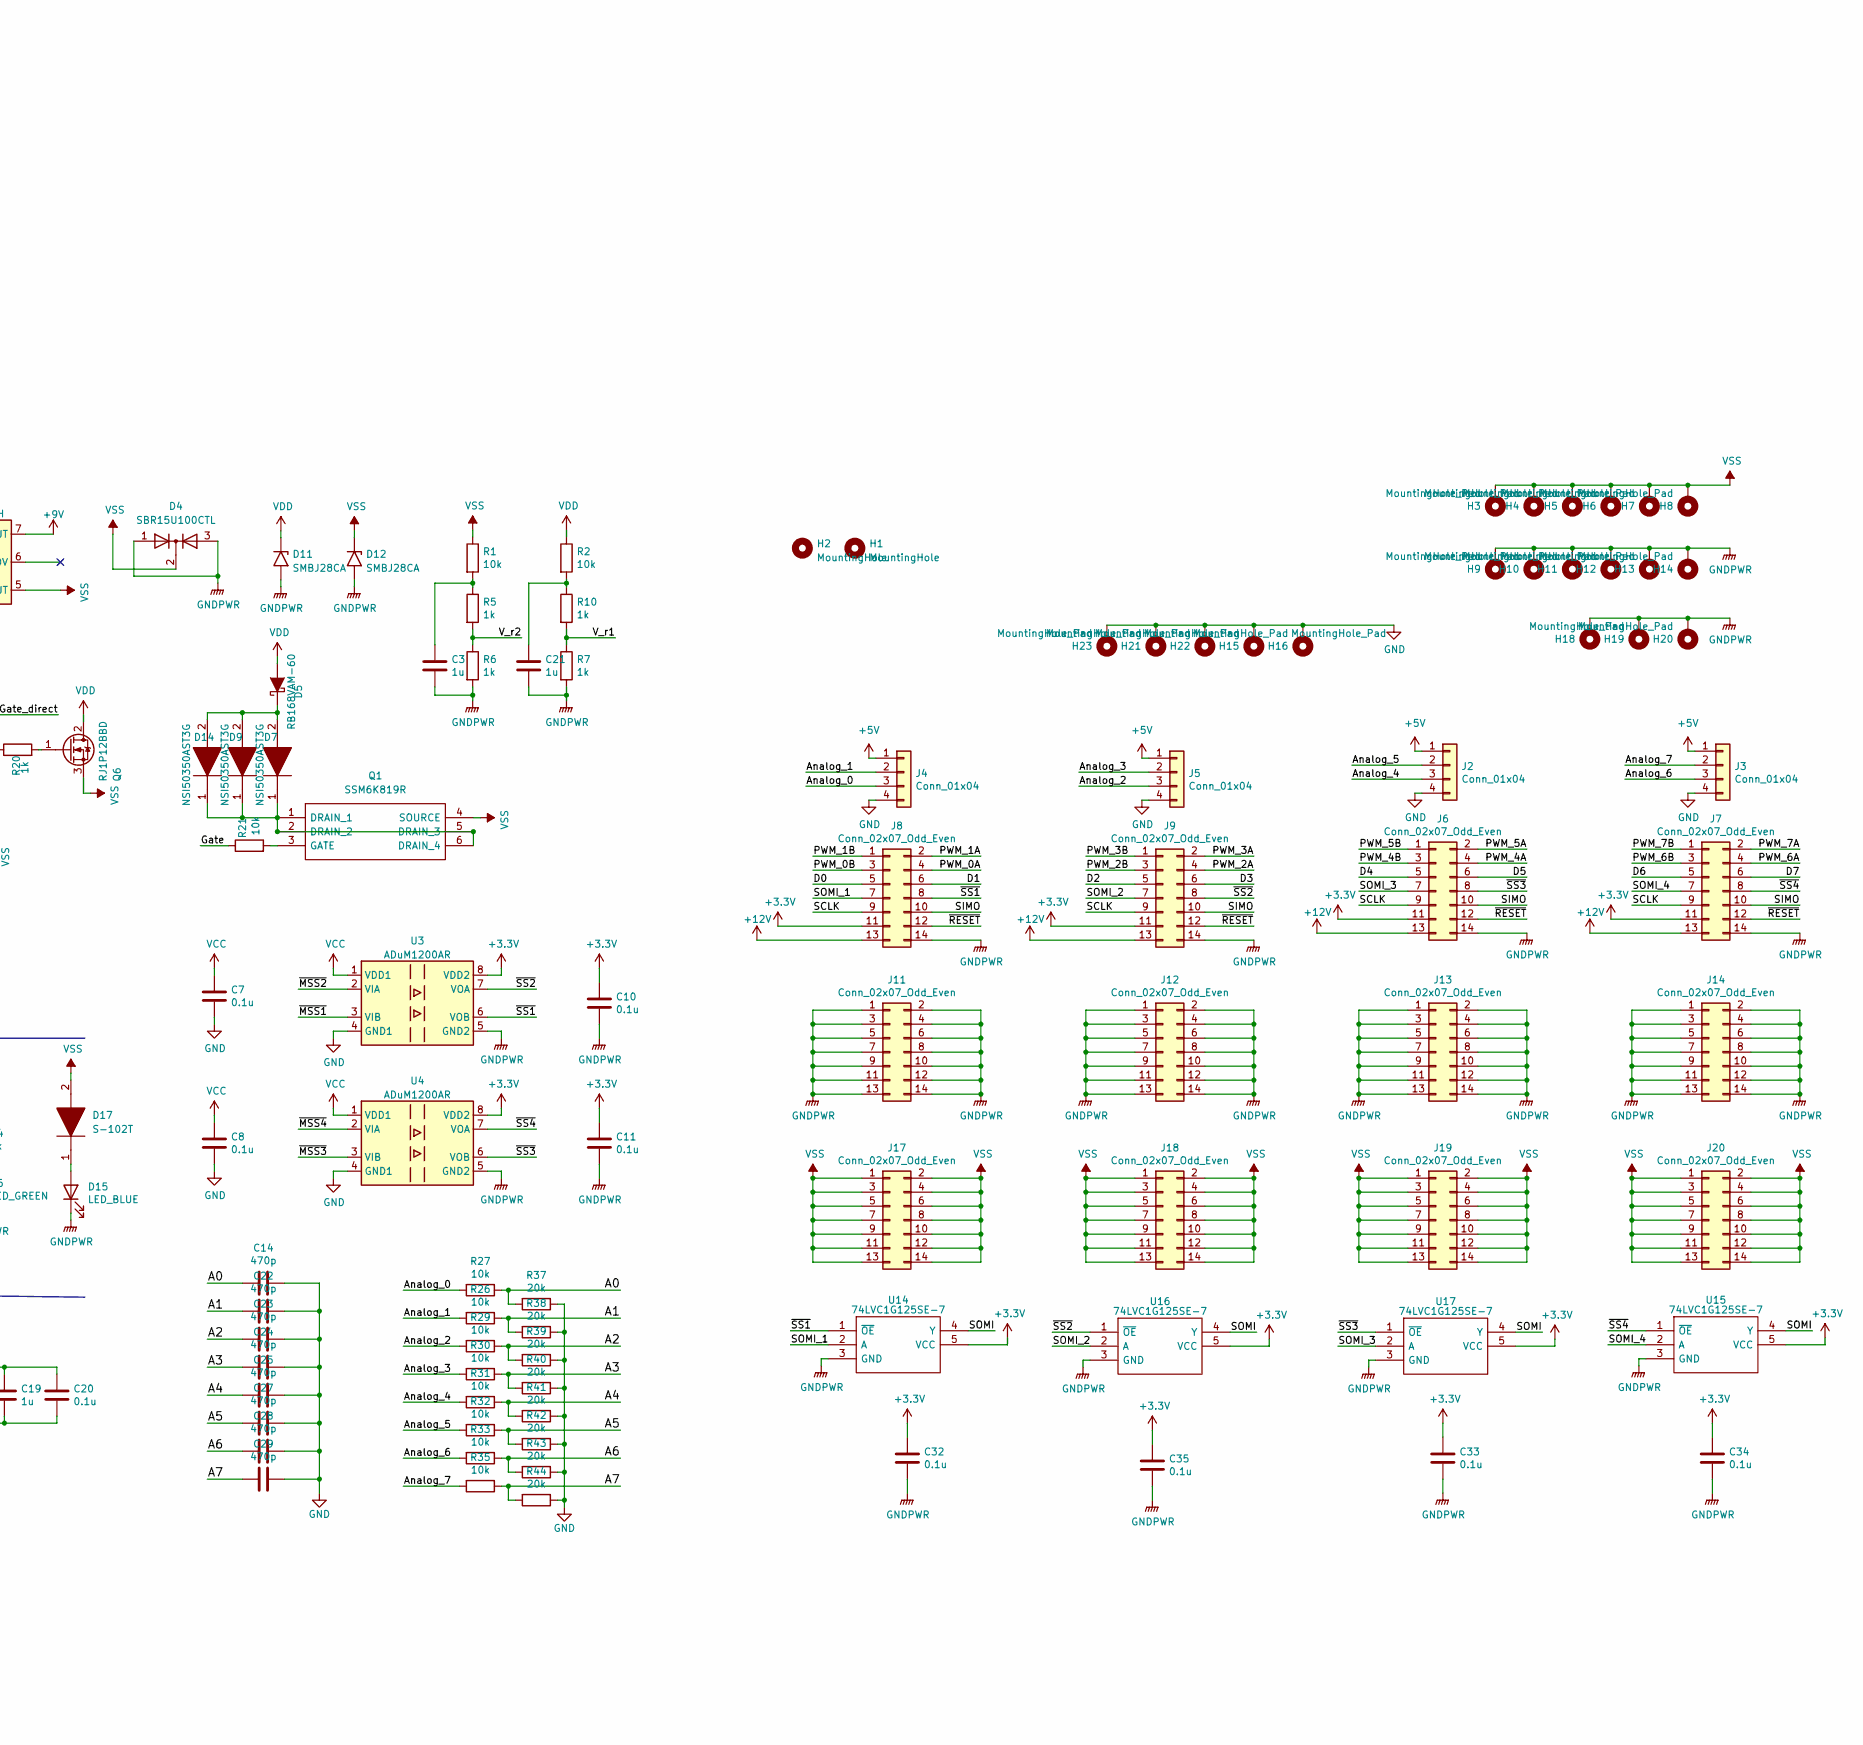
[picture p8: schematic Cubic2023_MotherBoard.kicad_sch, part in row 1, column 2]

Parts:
BZ1: UDB-05LFPN; Buzzer_12x9.5RM7.6
C1, C7, C8, C9, C10, C11, C13, C15, C16, C20, C26, C32, C33, C34, C35, C36, C37, C38: 0.1u; C_0402_1005Metric_Pad0.74x0.62mm_HandSolder; LCSC C307331
C2, C3, C5, C19, C21, C30, C31: 1u; C_0603_1608Metric; LCSC C15849
C4, C12, C17, C18: 10u; C_1206_3216Metric; LCSC C13585
C6: 10000u; CP_Radial_D25.0mm_P10.00mm_SnapIn
C14, C22, C23, C24, C25, C27, C28, C29: 470p; C_0603_1608Metric; LCSC C1620
D1, D13: LED_RED; LED_0603_1608Metric_Pad1.05x0.95mm_HandSolder; LCSC C2286
D2, D5, D10, D18: RB168VAM-60; CUHS20S40H3F
D3, D15: LED_BLUE; LED_0603_1608Metric_Pad1.05x0.95mm_HandSolder; LCSC C72041
D4: SBR15U100CTL; TO-252-2
D6: LED_GREEN; LED_0603_1608Metric_Pad1.05x0.95mm_HandSolder; LCSC C72043
D7, D9, D14: NSI50350AST3G; DIOM7958X256N; Manufacturer_Part_Number NSI50350AST3G; Mouser Part Number 863-NSI50350AST3G
D11, D12, D19: SMBJ28CA; D_SMB
D16: LED_YELLOW; LED_0603_1608Metric_Pad1.05x0.95mm_HandSolder; LCSC C72038
D17: S-102T; SODFL3516X70N; Manufacturer_Part_Number S-102T; Mouser Part Number 954-S-102T
F1: 1.1A/2.2A; Fuse_BelFuse_0ZRE0016FF_L9.9mm_W3.8mm
H1, H2: MountingHole; MountingHole_3.2mm_M3
H3, H4, H5, H6, H7, H8, H9, H10, H11, H12, H13, H14, H15, H16, H18, H19, H20, H21, H22, H23: MountingHole_Pad; MountingHole_2.2mm_M2_DIN965_Pad
IC1: ADUM3153ARSZ; ADUM3153; Manufacturer_Part_Number ADUM3153ARSZ; Mouser Part Number 584-ADUM3153ARSZ
J1: Conn_02x06_Odd_Even; PinSocket_2x06_P2.54mm_Vertical
J2, J3, J4, J5: Conn_01x04; PinSocket_1x04_P2.54mm_Vertical
J6, J7, J8, J9, J11, J12, J13, J14, J17, J18, J19, J20: Conn_02x07_Odd_Even; PinSocket_2x07_P2.54mm_Vertical
J10, J22, J23: Conn_02x06_Odd_Even; PinHeader_2x06_P1.27mm_Vertical
J15: Conn_01x02_Male; T_plug_male_diagonal
J16: Conn_01x06; PinSocket_1x06_P2.54mm_Vertical
Q1: SSM6K819R; SOTFL95P280X88-6N; Manufacturer_Part_Number SSM6K819R; Mouser Part Number N/A
Q2, Q3, Q4, Q5: BSS138; SOT-23
Q6: RJ1P12BBD; TO-263-2
R1, R2, R4, R18, R21, R25, R26, R27, R28, R29, R30, R31, R32, R33, R34, R35, R48, R50: 10k; R_0603_1608Metric; LCSC C25804
R3, R5, R6, R7, R10, R12, R16, R20, R22, R24, R45: 1k; R_0603_1608Metric; LCSC C21190
R8: 220; R_0603_1608Metric; LCSC C22962
R9, R19: 47k; R_0603_1608Metric; LCSC C25819
R11: 6.2k; R_0603_1608Metric; LCSC C25804
R13, R14: 75k; R_0603_1608Metric; LCSC C23242
R15, R36: 2.4k; R_0603_1608Metric; LCSC C22940
R17: 100k; R_0603_1608Metric; LCSC C25803
R23, R47: 3.3k; R_0603_1608Metric; LCSC C22978
R37, R38, R39, R40, R41, R42, R43, R44: 20k; R_0603_1608Metric; LCSC C4184
R46, R49: 1M; R_0603_1608Metric; LCSC C22935
TH1: Thermistor_100k; R_0603_1608Metric
U1: TLP293-4; SO-16_5.3x10.2mm_P1.27mm
U2, U7: NJU7109F; SOT-23-5
U3, U4: ADuM1200AR; SOIC-8_3.9x4.9mm_P1.27mm
U5, U13: TLP291; SOIC-4_4.55x2.6mm_P1.27mm
U6: NJM2396F33; TO-220-4_Horizontal_TabUp; Manufacturer_Part_Number NJM2396F33; Mouser Part Number 513-NJM2396F33
U8: MAPU01-033S09H; MAPU01
U9: M78AR12-1; TO-220-3_Vertical
U10, U12, U14, U15, U16, U17, U18: 74LVC1G125SE-7; SOT-353_SC-70-5; Manufacturer_Part_Number 74LVC1G125SE-7; Mouser Part Number 621-74LVC1G125SE-7
U11: MCP3208; SOIC-16_3.9x9.9mm_P1.27mm

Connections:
+5V: J1.7, J2.1, J3.1, J4.1, J5.1
+9V: U5.4, U8.7 (+VOUT)
+12V: C5.1, C12.1, C16.1, D2.1 (K), D10.1 (K), J6.13, J7.13, J8.13, J9.13, U6.1 (VIN), U6.4 (ON/OFF_CONTROL), U9.3 (OUT)
/A0: C14.1, R27.1, R37.2, U11.6 (CH5)
/A1: C22.1, R26.1, R38.2, U11.8 (CH7)
/A2: C23.1, R29.1, R39.2, U11.5 (CH4)
/A3: C24.1, R30.1, R40.2, U11.7 (CH6)
/A4: C25.1, R31.1, R41.2, U11.3 (CH2)
/A5: C27.1, R32.1, R42.2, U11.4 (CH3)
/A6: C28.1, R33.1, R43.2, U11.2 (CH1)
/A7: C29.1, R35.1, R44.2, U11.1 (CH0)
/Analog_0: J4.3, R27.2
/Analog_1: J4.2, R26.2
/Analog_2: J5.3, R29.2
/Analog_3: J5.2, R30.2
/Analog_4: J2.3, R31.2
/Analog_5: J2.2, R32.2
/Analog_6: J3.3, R33.2
/Analog_7: J3.2, R35.2
/D0: J8.5, J23.11
/D1: J8.6, J23.12
/D2: J9.5, J23.8
/D3: J9.6, J23.10
/D4: J6.5, J22.12
/D5: J6.6, J22.11
/D6: J7.5, J22.1
/D7: J7.6, J22.2
/GPIO0: IC1.17 (SI), J6.10, J7.10, J8.10, J9.10, J10.3, J10.4
/GPIO1: IC1.15 (~SSS), J10.1, U18.1 (~OE)
/GPIO2: IC1.18 (SCLK), J6.9, J7.9, J8.9, J9.9, J10.2
/GPIO3: J10.6, U18.2 (A)
/GPIO6: J7.3, J22.4
/GPIO7: J7.4, J22.6
/GPIO8: J7.1, J22.8
/GPIO9: J7.2, J22.10
/GPIO12: J6.3, J22.9
/GPIO13: J6.4, J22.7
/GPIO14: J6.1, J22.5
/GPIO15: J6.2, J22.3
/GPIO16: J8.2, J23.5
/GPIO17: J8.1, J23.3
/GPIO18: J9.3, J23.1
/GPIO19: J9.4, J23.2
/GPIO20: J9.1, J23.4
/GPIO21: J9.2, J23.6
/GPIO26: J8.4, J23.9
/GPIO27: J8.3, J23.7
/GPIO28: J10.11, R5.2, R6.1, U7.1 (-)
/GPIO29: J10.9, R7.1, R10.2, U2.1 (-)
/Gate: R21.1, R28.1, U5.3
/Gate_LED: D16.2 (A), R19.1, R28.2, R50.1
/Gate_direct: D16.1 (K), R20.1, R50.2, U13.4
/MCLK: IC1.3 (MCLK), J1.3, U11.13 (CLK)
/MISO: J16.4, U11.12 (Dout)
/MISO_A: IC1.5 (MI), J1.5
/MOSI: IC1.4 (MO), J1.6, U11.11 (Din)
/SOMI: IC1.16 (SO), U14.4 (Y), U15.4 (Y), U16.4 (Y), U17.4 (Y), U18.4 (Y)
/SOMI_1: J8.7, U14.2 (A)
/SOMI_2: J9.7, U16.2 (A)
/SOMI_3: J6.7, U17.2 (A)
/SOMI_4: J7.7, U15.2 (A)
/buzzer_0: R13.2, R24.1, R25.1, R46.1, U2.4
/buzzer_1: R12.1, U1.5, U1.9
/~ADC_SS: J16.3, U11.10 (~CS/SHDN)
/~MSS0: IC1.6 (~MSS), J1.8
/~MSS1: J1.9, U3.3 (VIB)
/~MSS2: J1.11, U3.2 (VIA)
/~MSS3: J16.1, U4.3 (VIB)
/~MSS4: J16.2, U4.2 (VIA)
/~RESET: J6.12, J7.12, J8.12, J9.12, J10.12, Q4.1 (G), Q5.1 (G), R3.2
/~SD: U1.4, U1.12, U1.16, U5.1
/~SHUTOUT: J1.4, R16.2
/~SS1: J8.8, U3.6 (VOB), U14.1 (~OE)
/~SS2: J9.8, U3.7 (VOA), U16.1 (~OE)
/~SS3: J6.8, U4.6 (VOB), U17.1 (~OE)
/~SS4: J7.8, U4.7 (VOA), U15.1 (~OE)
GND: C1.2, C7.2, C8.2, C14.2, C22.2, C23.2, C24.2, C25.2, C26.2, C27.2, C28.2, C29.2, H15.1, H16.1, H21.1, H22.1, H23.1, IC1.2 (GND1_1), IC1.7 (VOA), IC1.8 (VOB), IC1.9 (VOC), IC1.10 (GND1_2), J1.2, J1.10, J1.12, J2.4, J3.4, J4.4, J5.4, J16.5, J16.6, R37.1, R38.1, R39.1, R40.1, R41.1, R42.1, R43.1, R44.1, U1.11, U1.15, U3.4 (GND1), U4.4 (GND1), U5.2, U11.9 (DGND), U11.14 (AGND)
GNDPWR: C2.1, C3.2, C4.2, C5.2, C6.2, C9.2, C10.2, C11.2, C12.2, C13.2, C15.2, C16.2, C17.2, C18.2, C19.2, C20.2, C21.2, C30.1, C31.1, C32.2, C33.2, C34.2, C35.2, C36.2, C37.2, C38.2, D4.1 (A), D4.3 (A), D6.1 (K), D11.2 (A2), D12.2 (A2), D13.1 (K), D15.1 (K), D19.2 (A2), H9.1, H10.1, H11.1, H12.1, H13.1, H14.1, H18.1, H19.1, H20.1, IC1.11 (GND2_1), IC1.12 (VIC), IC1.13 (VIB), IC1.14 (VIA), IC1.19 (GND2_2), J6.14, J7.14, J8.14, J9.14, J10.7, J10.8, J11.1, J11.2, J11.3, J11.4, J11.5, J11.6, J11.7, J11.8, J11.9, J11.10, J11.11, J11.12, J11.13, J11.14, J12.1, J12.2, J12.3, J12.4, J12.5, J12.6, J12.7, J12.8, J12.9, J12.10, J12.11, J12.12, J12.13, J12.14, J13.1, J13.2, J13.3, J13.4, J13.5, J13.6, J13.7, J13.8, J13.9, J13.10, J13.11, J13.12, J13.13, J13.14, J14.1, J14.2, J14.3, J14.4, J14.5, J14.6, J14.7, J14.8, J14.9, J14.10, J14.11, J14.12, J14.13, J14.14, J15.2, Q2.2 (S), Q3.2 (S), Q4.2 (S), R4.1, R6.2, R7.2, R11.1, R17.1, R23.2, R47.2, U1.2, U2.2 (V-), U3.5 (GND2), U4.5 (GND2), U6.3 (GND), U7.2 (V-), U8.2 (-VIN), U9.2 (GND), U10.1 (~OE), U10.3 (GND), U12.1 (~OE), U12.3 (GND), U13.2, U14.3 (GND), U15.3 (GND), U16.3 (GND), U17.3 (GND), U18.3 (GND)
unnamed: BZ1.2 (+), D1.1 (K), Q5.3 (D)
unnamed: C2.2, R11.2, TH1.1, U1.6, U1.7
unnamed: C3.1, R1.2, R5.1
unnamed: C21.1, R2.2, R10.1
unnamed: C30.2, R46.2, U10.2 (A)
unnamed: C31.2, R48.2, R49.2, U12.2 (A)
unnamed: D1.2 (A), R18.1
unnamed: D3.2 (A), R9.1, R19.2
unnamed: D6.2 (A), R34.2
unnamed: D10.2 (A), J10.10
unnamed: D13.2 (A), R25.2
unnamed: D7.1, D9.1, D14.1, Q1.1 (DRAIN_1), Q1.2 (DRAIN_2), Q1.5 (DRAIN_3), Q1.6 (DRAIN_4)
unnamed: D5.1 (K), D7.2, D9.2, D14.2
unnamed: D15.2 (A), D17.1
unnamed: D18.1 (K), R14.2, R49.1, U7.4
unnamed: D18.2 (A), R48.1
unnamed: D19.1 (A1), F1.2, U9.1 (IN)
unnamed: Q1.3 (GATE), R21.2
unnamed: Q2.1 (G), R24.2
unnamed: Q2.3 (D), Q3.3 (D), Q5.2 (S)
unnamed: Q3.1 (G), R12.2, R17.2
unnamed: Q4.3 (D), R8.2
unnamed: Q6.1 (G), R20.2
unnamed: R3.1, R4.2, U1.13
unnamed: R8.1, U1.8
unnamed: R13.1, R36.2, R47.1, U2.3 (+)
unnamed: R14.1, R15.2, R23.1, U7.3 (+)
unnamed: R16.1, U1.3
unnamed: R22.1, U12.4 (Y)
unnamed: R22.2, U13.1
unnamed: R45.1, U10.4 (Y)
unnamed: R45.2, U1.1
VCC: C1.1, C7.1, C8.1, C26.1, IC1.1 (VDD1), J1.1, U3.1 (VDD1), U4.1 (VDD1), U11.15 (Vref), U11.16 (Vdd)
VDD: C4.1, D5.2 (A), D11.1 (A1), F1.1, J15.1, Q6.2 (D), R2.1
VSS: C6.1, D3.1 (K), D4.2 (K), D12.1 (A1), D17.2, H3.1, H4.1, H5.1, H6.1, H7.1, H8.1, J17.1, J17.2, J17.3, J17.4, J17.5, J17.6, J17.7, J17.8, J17.9, J17.10, J17.11, J17.12, J17.13, J17.14, J18.1, J18.2, J18.3, J18.4, J18.5, J18.6, J18.7, J18.8, J18.9, J18.10, J18.11, J18.12, J18.13, J18.14, J19.1, J19.2, J19.3, J19.4, J19.5, J19.6, J19.7, J19.8, J19.9, J19.10, J19.11, J19.12, J19.13, J19.14, J20.1, J20.2, J20.3, J20.4, J20.5, J20.6, J20.7, J20.8, J20.9, J20.10, J20.11, J20.12, J20.13, J20.14, Q1.4 (SOURCE), Q6.3 (S), R1.1, R9.2, U8.5 (-VOUT), U13.3

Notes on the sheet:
High to Low 1.935V Low to High 1.875V
PWM6
PWM2
PWM0
PWM1
PWM4
PWM5
PWM7
PWM3
regulator
condenser

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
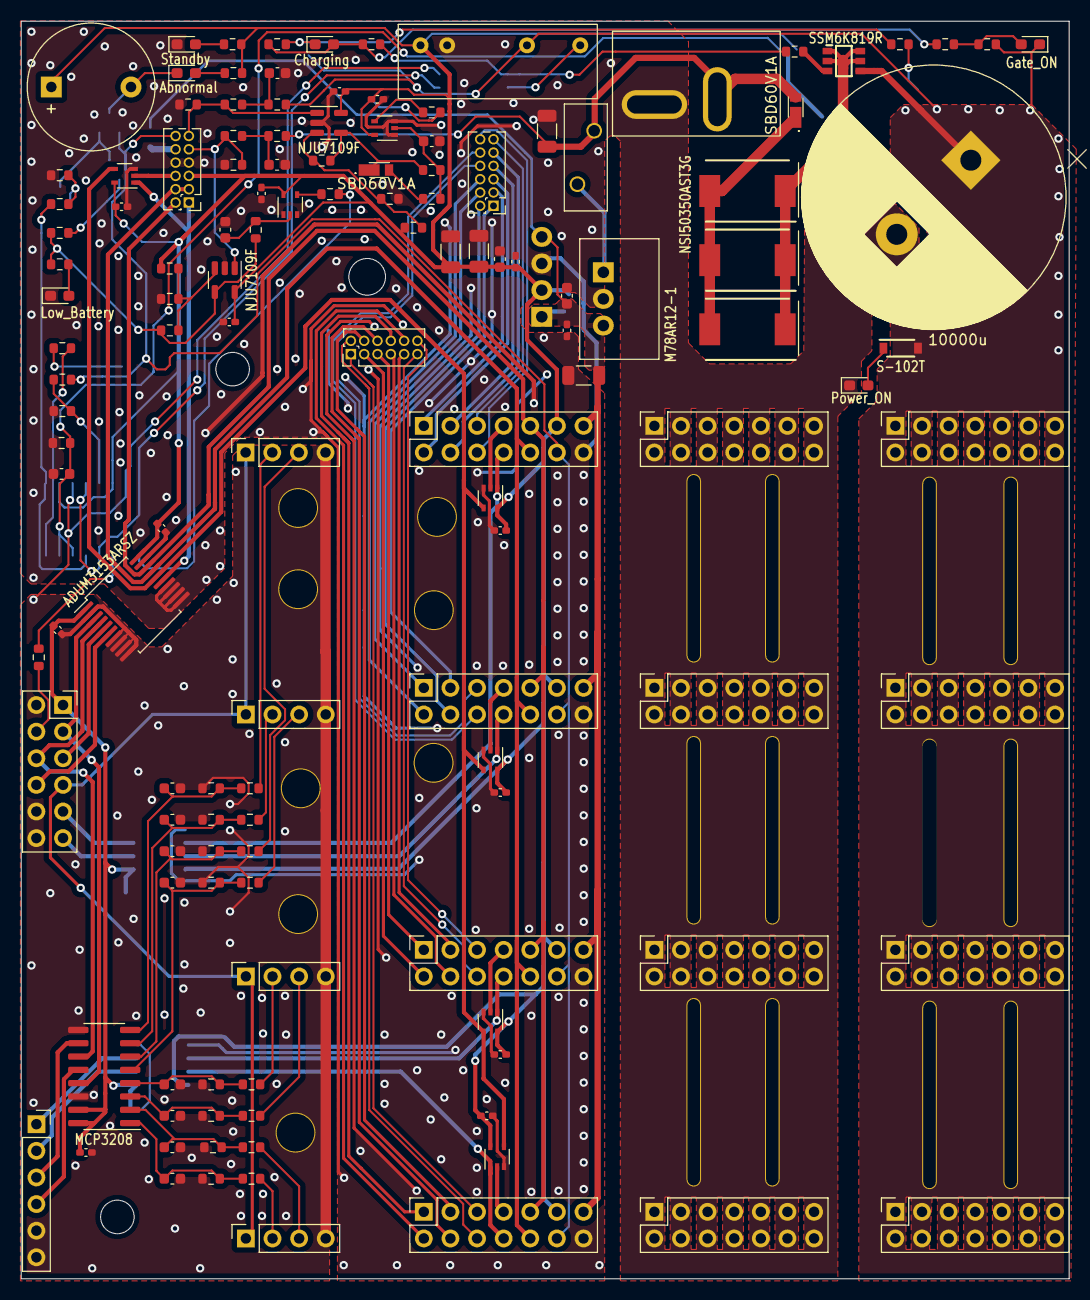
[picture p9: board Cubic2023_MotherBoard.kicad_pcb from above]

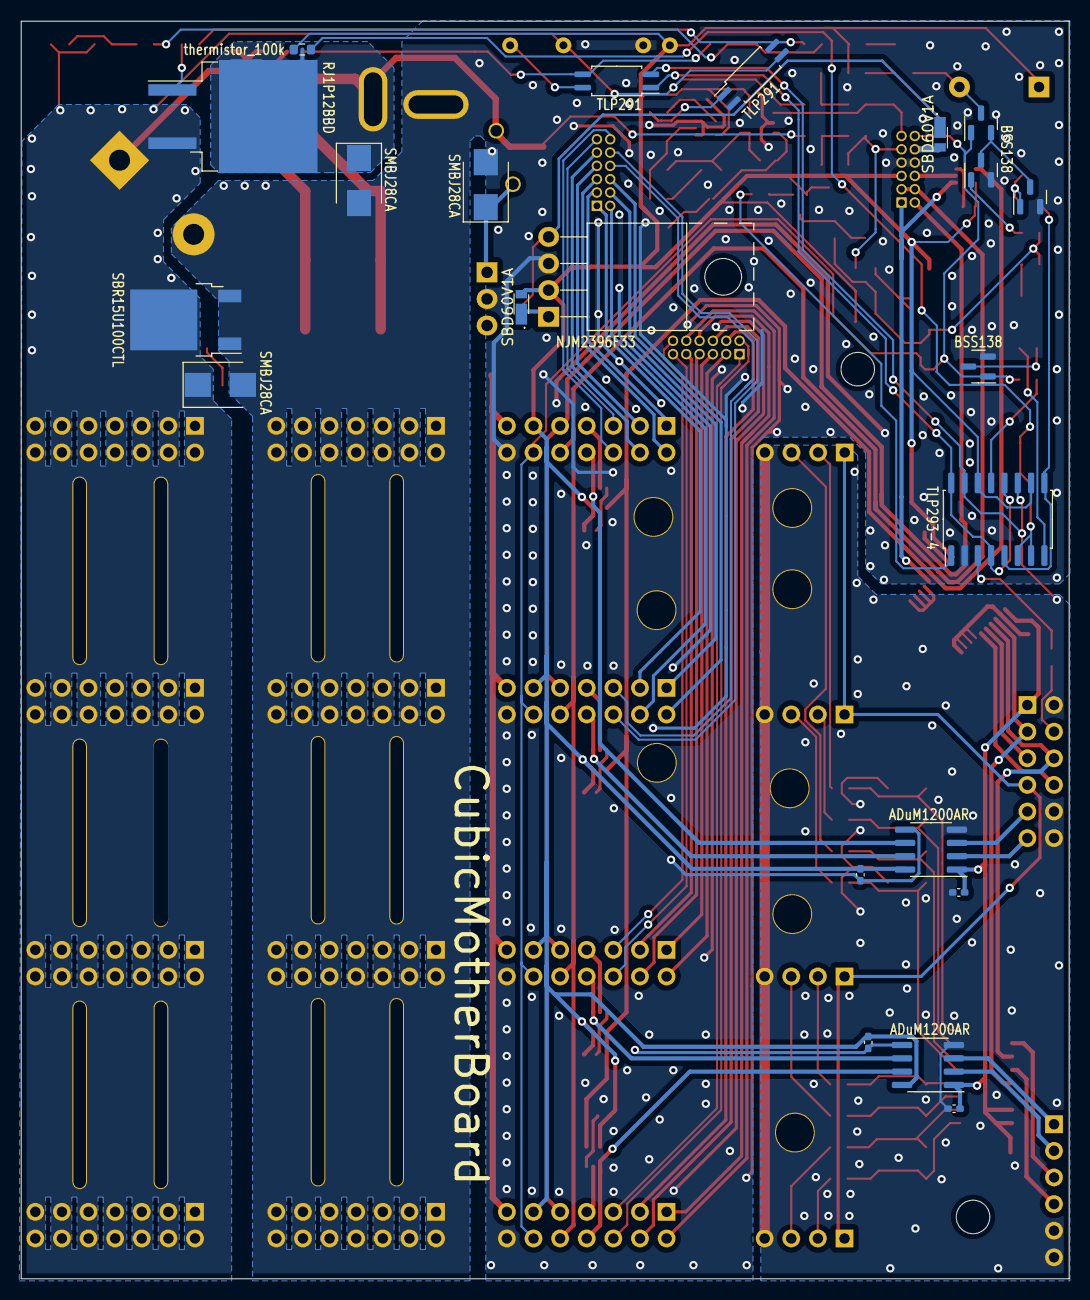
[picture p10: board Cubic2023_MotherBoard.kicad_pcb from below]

Board: 2 copper layers, 100.0 x 120.0 mm, 178 parts (22 on the bottom side), 114 nets.

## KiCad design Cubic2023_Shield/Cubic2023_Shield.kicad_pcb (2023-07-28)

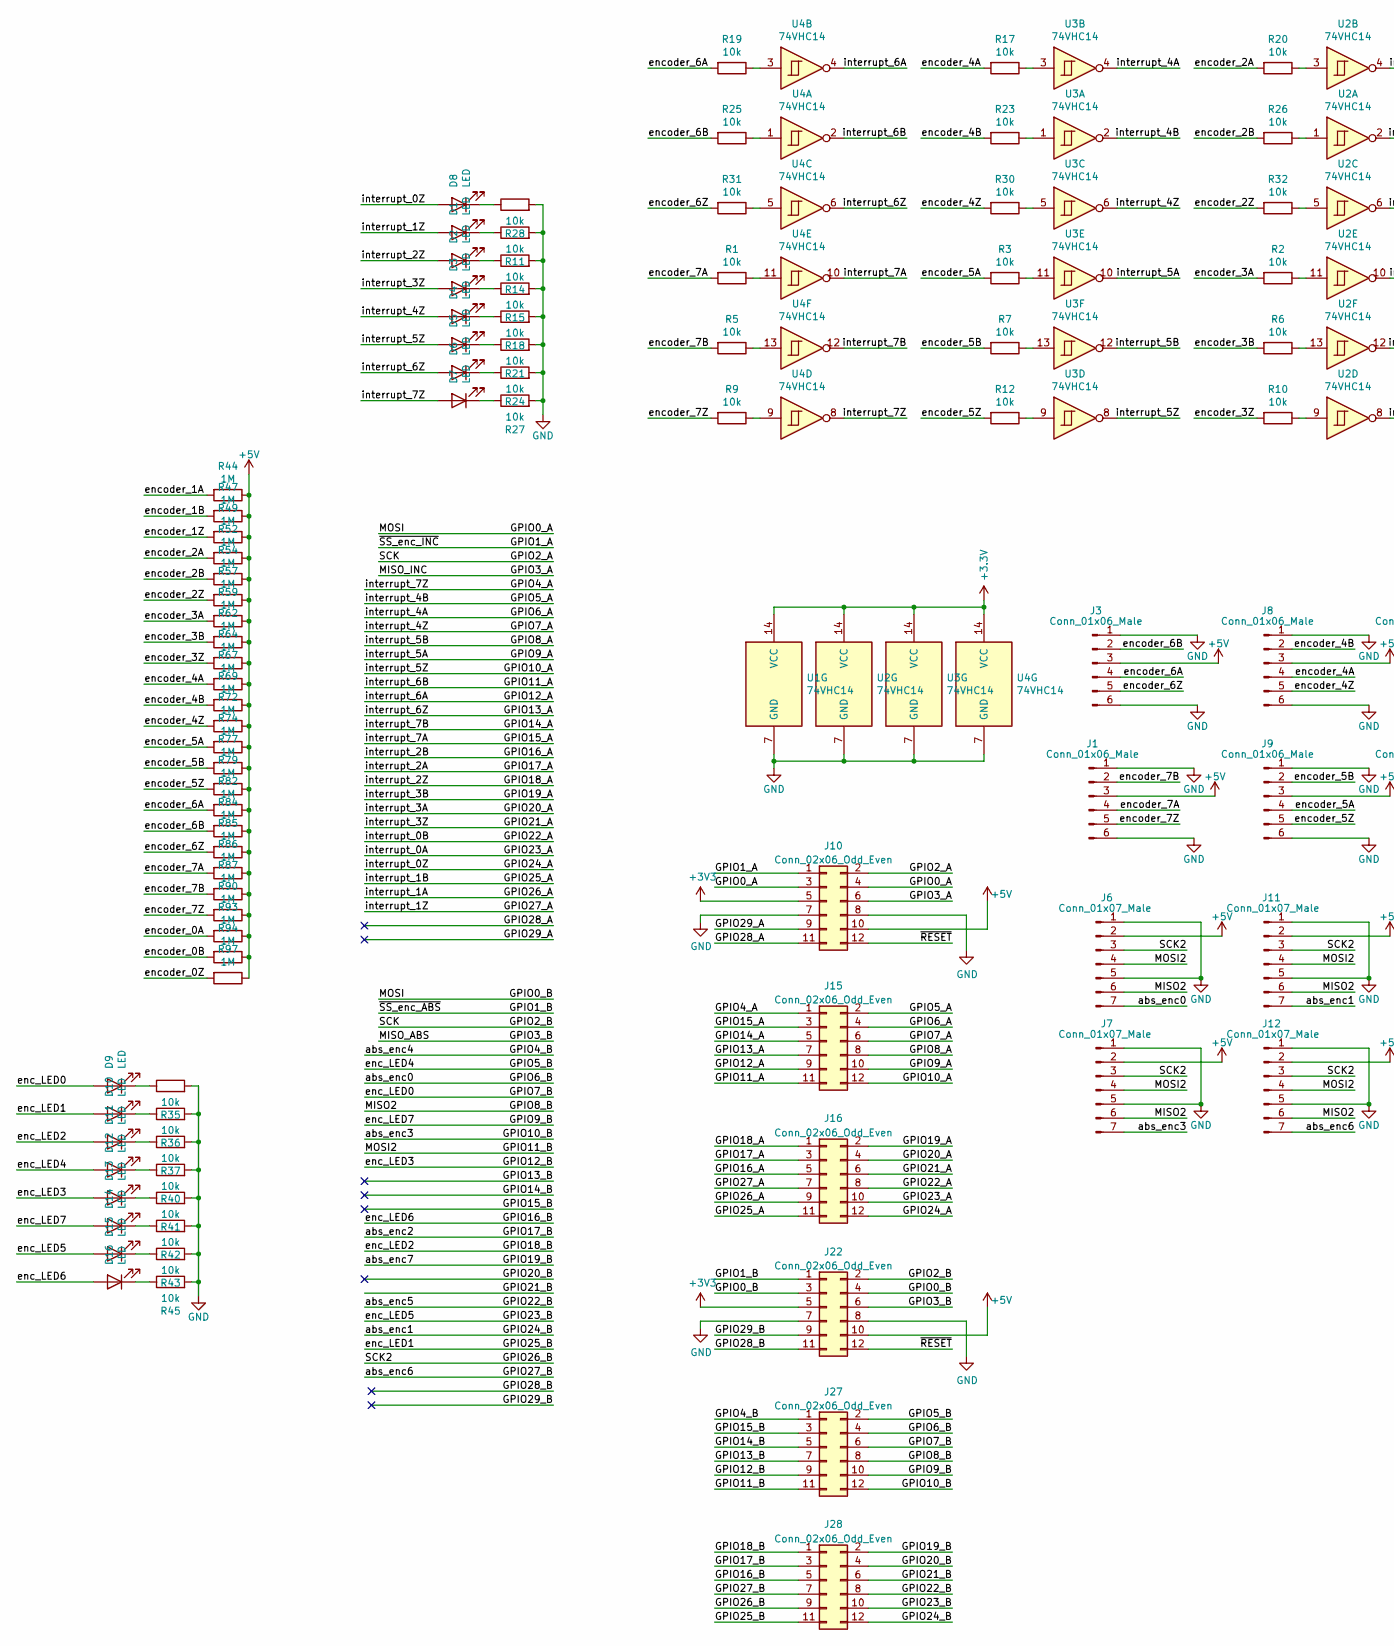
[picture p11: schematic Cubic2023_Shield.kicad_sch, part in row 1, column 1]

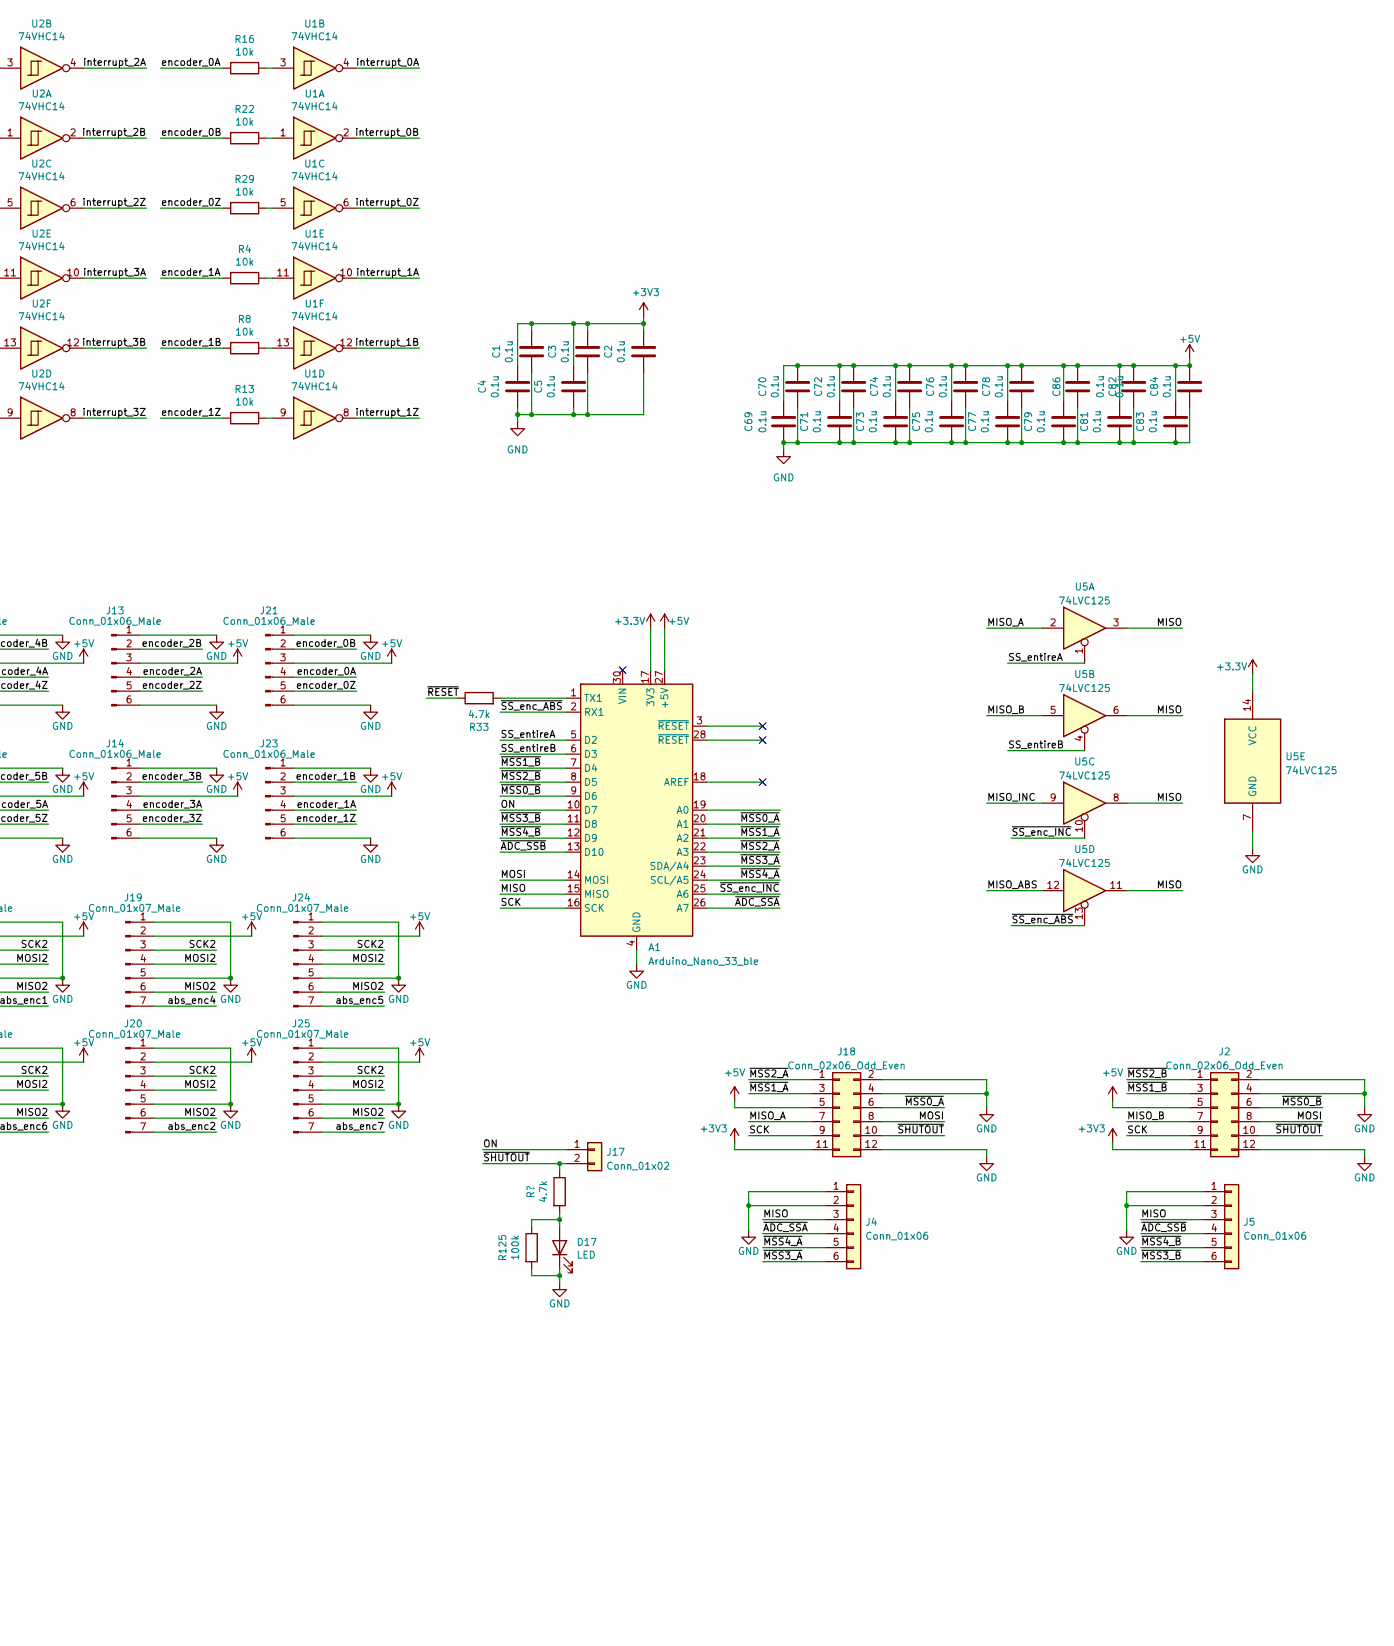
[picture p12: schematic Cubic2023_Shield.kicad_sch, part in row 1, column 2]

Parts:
A1: Arduino_Nano_33_ble; Arduino_Nano
C1, C2, C3, C4, C5, C69, C70, C71, C72, C73, C74, C75, C76, C77, C78, C79, C81, C82, C83, C84, C86: 0.1u; C_0402_1005Metric_Pad0.74x0.62mm_HandSolder; LCSC C307331
D1, D2, D3, D4, D5, D6, D7, D8, D9, D10, D11, D12, D13, D14, D15, D16, D17: LED; LED_0603_1608Metric_Pad1.05x0.95mm_HandSolder; LCSC C72041
J1, J3, J8, J9, J13, J14, J21, J23: Conn_01x06_Male; PinSocket_1x06_P2.00mm_Vertical
J2, J18: Conn_02x06_Odd_Even; PinSocket_2x06_P2.54mm_Horizontal
J4, J5: Conn_01x06; PinSocket_1x06_P2.54mm_Horizontal
J6, J7, J11, J12, J19, J20, J24, J25: Conn_01x07_Male; PinSocket_1x07_P2.00mm_Vertical
J10, J15, J16, J22, J27, J28: Conn_02x06_Odd_Even; PinHeader_2x06_P1.27mm_Vertical
J17: Conn_01x02; PinSocket_1x02_P2.54mm_Vertical
R1, R2, R3, R4, R5, R6, R7, R8, R9, R10, R11, R12, R13, R14, R15, R16, R17, R18, R19, R20, R21, R22, R23, R24, R25, R26, R27, R28, R29, R30, R31, R32, R35, R36, R37, R40, R41, R42, R43, R45: 10k; R_0603_1608Metric; LCSC C25804
R33: 4.7k; R_0603_1608Metric
R44, R47, R49, R52, R54, R57, R59, R62, R64, R67, R69, R72, R74, R77, R79, R82, R84, R85, R86, R87, R90, R93, R94, R97: 1M; R_0603_1608Metric; LCSC C22935
R125: 100k; R_0603_1608Metric; LCSC C25803
U1, U2, U3, U4: 74VHC14; TSSOP-14_4.4x5mm_P0.65mm; LCSC C6145
U5: 74LVC125; SO-14_3.9x8.65mm_P1.27mm; LCSC C460512

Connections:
+5V: A1.27 (+5V), C69.2, C70.2, C71.2, C72.2, C73.2, C74.2, C75.2, C76.2, C77.2, C78.2, C79.2, C81.2, C82.2, C83.2, C84.2, C86.2, J1.3, J2.5, J3.3, J6.2, J7.2, J8.3, J9.3, J10.10, J11.2, J12.2, J13.3, J14.3, J18.5, J19.2, J20.2, J21.3, J22.10, J23.3, J24.2, J25.2, R44.1, R47.1, R49.1, R52.1, R54.1, R57.1, R59.1, R62.1, R64.1, R67.1, R69.1, R72.1, R74.1, R77.1, R79.1, R82.1, R84.1, R85.1, R86.1, R87.1, R90.1, R93.1, R94.1, R97.1
/GPIO0_A: A1.14 (MOSI), J2.8, J10.3, J10.4, J18.8, J22.3, J22.4
/GPIO1_A: A1.25 (A6), J10.1, U5.10
/GPIO1_B: A1.2 (RX1), J22.1, U5.13
/GPIO2_A: A1.16 (SCK), J2.9, J10.2, J18.9, J22.2
/GPIO3_A: J10.6, U5.9
/GPIO3_B: J22.6, U5.12
/GPIO4_A: D7.2 (A), J15.1, U4.8
/GPIO4_B: J19.7, J27.1
/GPIO5_A: J15.2, U3.2
/GPIO5_B: D12.2 (A), J27.2
/GPIO6_A: J15.4, U3.4
/GPIO6_B: J6.7, J27.4
/GPIO7_A: D4.2 (A), J15.6, U3.6
/GPIO7_B: D9.2 (A), J27.6
/GPIO8_A: J15.8, U3.12
/GPIO8_B: J6.6, J7.6, J11.6, J12.6, J19.6, J20.6, J24.6, J25.6, J27.8
/GPIO9_A: J15.10, U3.10
/GPIO9_B: D14.2 (A), J27.10
/GPIO10_A: D5.2 (A), J15.12, U3.8
/GPIO10_B: J7.7, J27.12
/GPIO11_A: J15.11, U4.2
/GPIO11_B: J6.4, J7.4, J11.4, J12.4, J19.4, J20.4, J24.4, J25.4, J27.11
/GPIO12_A: J15.9, U4.4
/GPIO12_B: D13.2 (A), J27.9
/GPIO13_A: D6.2 (A), J15.7, U4.6
/GPIO13_B: J27.7
/GPIO14_A: J15.5, U4.12
/GPIO14_B: J27.5
/GPIO15_A: J15.3, U4.10
/GPIO15_B: J27.3
/GPIO16_A: J16.5, U2.2
/GPIO16_B: D16.2 (A), J28.5
/GPIO17_A: J16.3, U2.4
/GPIO17_B: J20.7, J28.3
/GPIO18_A: D2.2 (A), J16.1, U2.6
/GPIO18_B: D11.2 (A), J28.1
/GPIO19_A: J16.2, U2.12
/GPIO19_B: J25.7, J28.2
/GPIO20_A: J16.4, U2.10
/GPIO20_B: J28.4
/GPIO21_A: D3.2 (A), J16.6, U2.8
/GPIO21_B: J28.6
/GPIO22_A: J16.8, U1.2
/GPIO22_B: J24.7, J28.8
/GPIO23_A: J16.10, U1.4
/GPIO23_B: D15.2 (A), J28.10
/GPIO24_A: D8.2 (A), J16.12, U1.6
/GPIO24_B: J11.7, J28.12
/GPIO25_A: J16.11, U1.12
/GPIO25_B: D10.2 (A), J28.11
/GPIO26_A: J16.9, U1.10
/GPIO26_B: J6.3, J7.3, J11.3, J12.3, J19.3, J20.3, J24.3, J25.3, J28.9
/GPIO27_A: D1.2 (A), J16.7, U1.8
/GPIO27_B: J12.7, J28.7
/GPIO28_A: J10.11
/GPIO28_B: J22.11
/GPIO29_A: J10.9
/GPIO29_B: J22.9
/MISO: A1.15 (MISO), J4.3, J5.3, U5.3, U5.6, U5.8, U5.11
/MISO_A: J18.7, U5.2
/MISO_B: J2.7, U5.5
/ON: A1.10 (D7), J17.1
/SS_entireA: A1.5 (D2), U5.1
/SS_entireB: A1.6 (D3), U5.4
/encoder_0A: J21.4, R16.2, R93.2
/encoder_0B: J21.2, R22.2, R94.2
/encoder_0Z: J21.5, R29.2, R97.2
/encoder_1A: J23.4, R4.2, R44.2
/encoder_1B: J23.2, R8.2, R47.2
/encoder_1Z: J23.5, R13.2, R49.2
/encoder_2A: J13.4, R20.2, R52.2
/encoder_2B: J13.2, R26.2, R54.2
/encoder_2Z: J13.5, R32.2, R57.2
/encoder_3A: J14.4, R2.2, R59.2
/encoder_3B: J14.2, R6.2, R62.2
/encoder_3Z: J14.5, R10.2, R64.2
/encoder_4A: J8.4, R17.2, R67.2
/encoder_4B: J8.2, R23.2, R69.2
/encoder_4Z: J8.5, R30.2, R72.2
/encoder_5A: J9.4, R3.2, R74.2
/encoder_5B: J9.2, R7.2, R77.2
/encoder_5Z: J9.5, R12.2, R79.2
/encoder_6A: J3.4, R19.2, R82.2
/encoder_6B: J3.2, R25.2, R84.2
/encoder_6Z: J3.5, R31.2, R85.2
/encoder_7A: J1.4, R1.2, R86.2
/encoder_7B: J1.2, R5.2, R87.2
/encoder_7Z: J1.5, R9.2, R90.2
/~ADC_SSA: A1.26 (A7), J4.4
/~ADC_SSB: A1.13 (D10), J5.4
/~MSS0_A: A1.20 (A1), J18.6
/~MSS0_B: A1.9 (D6), J2.6
/~MSS1_A: A1.21 (A2), J18.3
/~MSS1_B: A1.7 (D4), J2.3
/~MSS2_A: A1.22 (A3), J18.1
/~MSS2_B: A1.8 (D5), J2.1
/~MSS3_A: A1.23 (SDA/A4), J4.6
/~MSS3_B: A1.11 (D8), J5.6
/~MSS4_A: A1.24 (SCL/A5), J4.5
/~MSS4_B: A1.12 (D9), J5.5
/~RESET: J10.12, J22.12, R33.1
/~SHUTOUT: J2.10, J17.2, J18.10; also elsewhere on the board
GND: A1.4 (GND), A1.29 (GND), C1.1, C2.1, C3.1, C4.1, C5.1, C69.1, C70.1, C71.1, C72.1, C73.1, C74.1, C75.1, C76.1, C77.1, C78.1, C79.1, C81.1, C82.1, C83.1, C84.1, C86.1, D17.1 (K), J1.1, J1.6, J2.2, J2.4, J2.12, J3.1, J3.6, J4.1, J4.2, J5.1, J5.2, J6.1, J6.5, J7.1, J7.5, J8.1, J8.6, J9.1, J9.6, J10.7, J10.8, J11.1, J11.5, J12.1, J12.5, J13.1, J13.6, J14.1, J14.6, J18.2, J18.4, J18.12, J19.1, J19.5, J20.1, J20.5, J21.1, J21.6, J22.7, J22.8, J23.1, J23.6, J24.1, J24.5, J25.1, J25.5, R11.2, R14.2, R15.2, R18.2, R21.2, R24.2, R27.2, R28.2, R35.2, R36.2, R37.2, R40.2, R41.2, R42.2, R43.2, R45.2, R125.2, U1.7 (GND), U2.7 (GND), U3.7 (GND), U4.7 (GND), U5.7 (GND)
unnamed: A1.1 (TX1), R33.2
unnamed: D1.1 (K), R11.1
unnamed: D2.1 (K), R14.1
unnamed: D3.1 (K), R15.1
unnamed: D4.1 (K), R18.1
unnamed: D5.1 (K), R21.1
unnamed: D6.1 (K), R24.1
unnamed: D7.1 (K), R27.1
unnamed: D8.1 (K), R28.1
unnamed: D9.1 (K), R35.1
unnamed: D10.1 (K), R36.1
unnamed: D11.1 (K), R37.1
unnamed: D12.1 (K), R40.1
unnamed: D13.1 (K), R41.1
unnamed: D14.1 (K), R42.1
unnamed: D15.1 (K), R43.1
unnamed: D16.1 (K), R45.1
unnamed 121: D17.2 (A), R125.1; also elsewhere on the board
unnamed: R1.1, U4.11
unnamed: R2.1, U2.11
unnamed: R3.1, U3.11
unnamed: R4.1, U1.11
unnamed: R5.1, U4.13
unnamed: R6.1, U2.13
unnamed: R7.1, U3.13
unnamed: R8.1, U1.13
unnamed: R9.1, U4.9
unnamed: R10.1, U2.9
unnamed: R12.1, U3.9
unnamed: R13.1, U1.9
unnamed: R16.1, U1.3
unnamed: R17.1, U3.3
unnamed: R19.1, U4.3
unnamed: R20.1, U2.3
unnamed: R22.1, U1.1
unnamed: R23.1, U3.1
unnamed: R25.1, U4.1
unnamed: R26.1, U2.1
unnamed: R29.1, U1.5
unnamed: R30.1, U3.5
unnamed: R31.1, U4.5
unnamed: R32.1, U2.5

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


Board: 2 copper layers, 120.0 x 100.0 mm, 138 parts (6 on the bottom side), 138 nets.

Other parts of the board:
R34: 4.7k; R_0603_1608Metric

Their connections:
/~SHUTOUT: R34.1; also elsewhere on the board
unnamed 121: R34.2; also elsewhere on the board
